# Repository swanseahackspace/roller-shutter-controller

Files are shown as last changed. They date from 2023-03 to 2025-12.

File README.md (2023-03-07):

# Table of Contents

- [Introduction](https://github.com/swanseahackspace/roller-shutter-controller/#introduction)
- [Hardware](https://github.com/swanseahackspace/roller-shutter-controller/#hardware)
- [Software](https://github.com/swanseahackspace/roller-shutter-controller/#software)
	- [Requirements](https://github.com/swanseahackspace/roller-shutter-controller/#requirements)
	- [Installation](https://github.com/swanseahackspace/roller-shutter-controller/#installation)
  
# Introduction
Roller Shutter RFID Access Control PCB. Uses an ESP-32-C3 (Lolin C3 Mini)

# Hardware

#### Enclosure
The PCB has been designed to fit into ide EL161 enclosure.

- [Technical Drawing](hardware/enclosure-dimensions.pdf)
- [Product Page](https://ide.es/eng/products/junction-boxes-and-mechanisms/ip65-ip67-junction-boxes/ref_EL161)

#### KiCad Renders
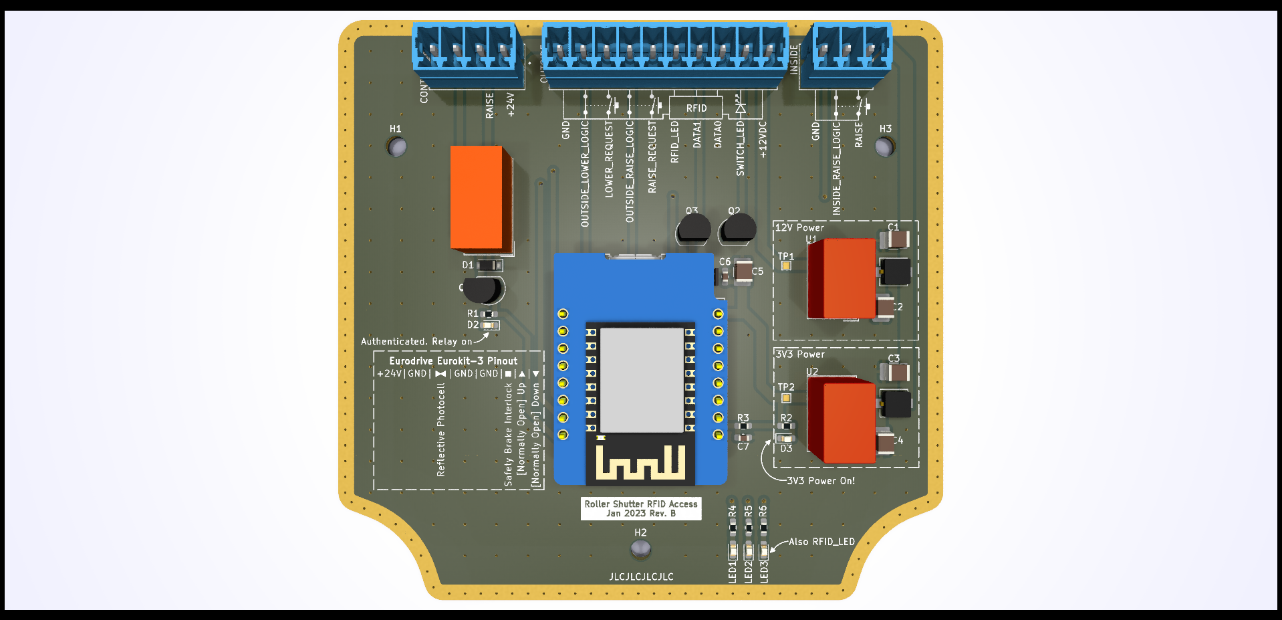
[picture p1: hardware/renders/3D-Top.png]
Top down 3D view

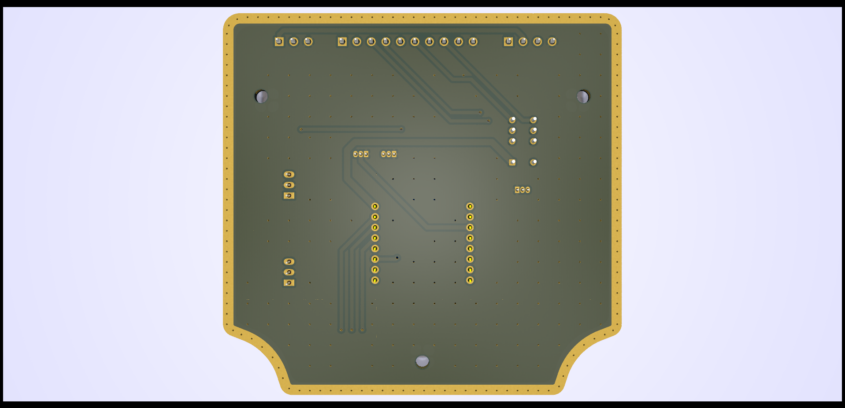
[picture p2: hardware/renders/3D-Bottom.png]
Bottom up 3D View


#### Assembly Render
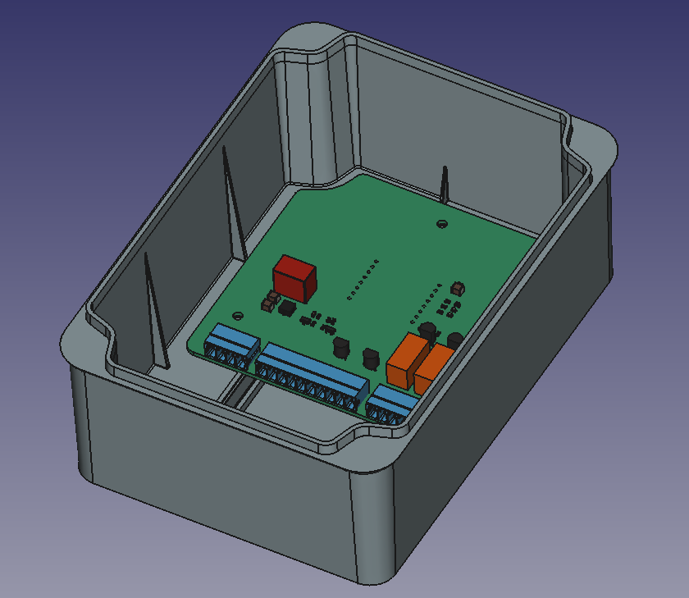
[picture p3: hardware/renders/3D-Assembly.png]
Assembly render


# Software
In the software folder you will find two programs:

- test is a simple script for doing hardware debugging. It provides a quick way to check that the LEDs are all working, and to toggle the relay on and off
- doorlock is a [submodule](https://git-scm.com/book/en/v2/Git-Tools-Submodules) of another git repo: https://github.com/swanseahackspace/doorlock. This is currently incompatable with this hardware, but will be modified to support both it's original hardware and the ESP-32-C3 via a flag in the config file.

### Requirements
- Arduino IDE or equivalent
- Arduino Libraries:
  - Adafruit Graphics
  - Adafruit SSD1306 Wemos Mini OLED

### Installation

1. Clone git repo
```
git clone https://github.com/swanseahackspace/roller-shutter-controller
```

2. Go into the doorlock directory
```
cd software/doorlock
```

3. Initialise the submodule
```
git submodule init
```

4. Update the submodule
```
git submodule update
```

5. Open .ino file in [Arduino IDE](https://www.arduino.cc/en/software)

6. Follow the [Wemos/Lolin C3 Mini Arduino development guide](https://www.wemos.cc/en/latest/tutorials/c3/get_started_with_arduino_c3.html)

7. Plug the board into your machine via the USB type-C port on the ESP-32-C3

8. Check the correct port is set in the Arduino IDE (Tools -> Port)

9. Upload the code to the ESP32

### Troubleshooting

*Errors uploading code to ESP-32-C3*
Use the following procedure:

- Hold on Button 9
- Press Button Reset
- Release Button 9 When you hear the prompt tone on usb reconnection

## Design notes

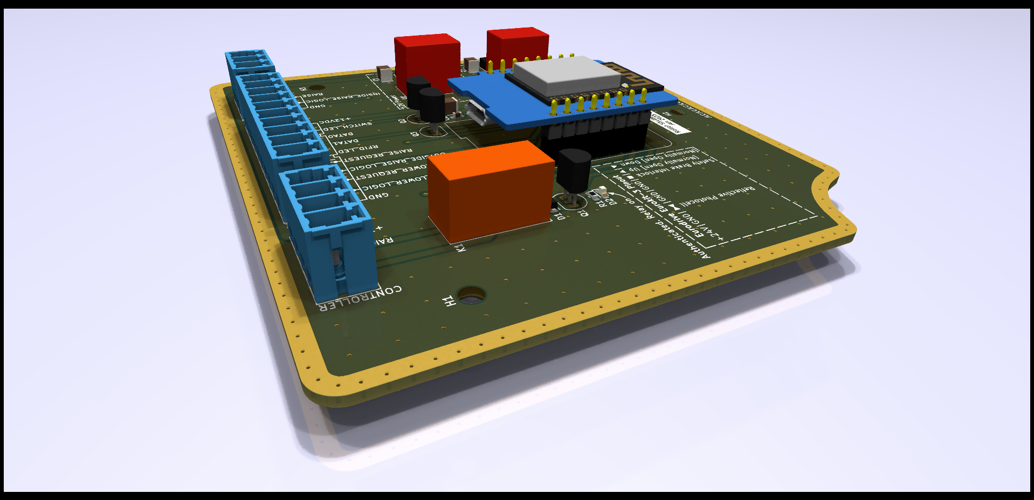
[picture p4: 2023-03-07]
hardware/renders/3D-3D.png

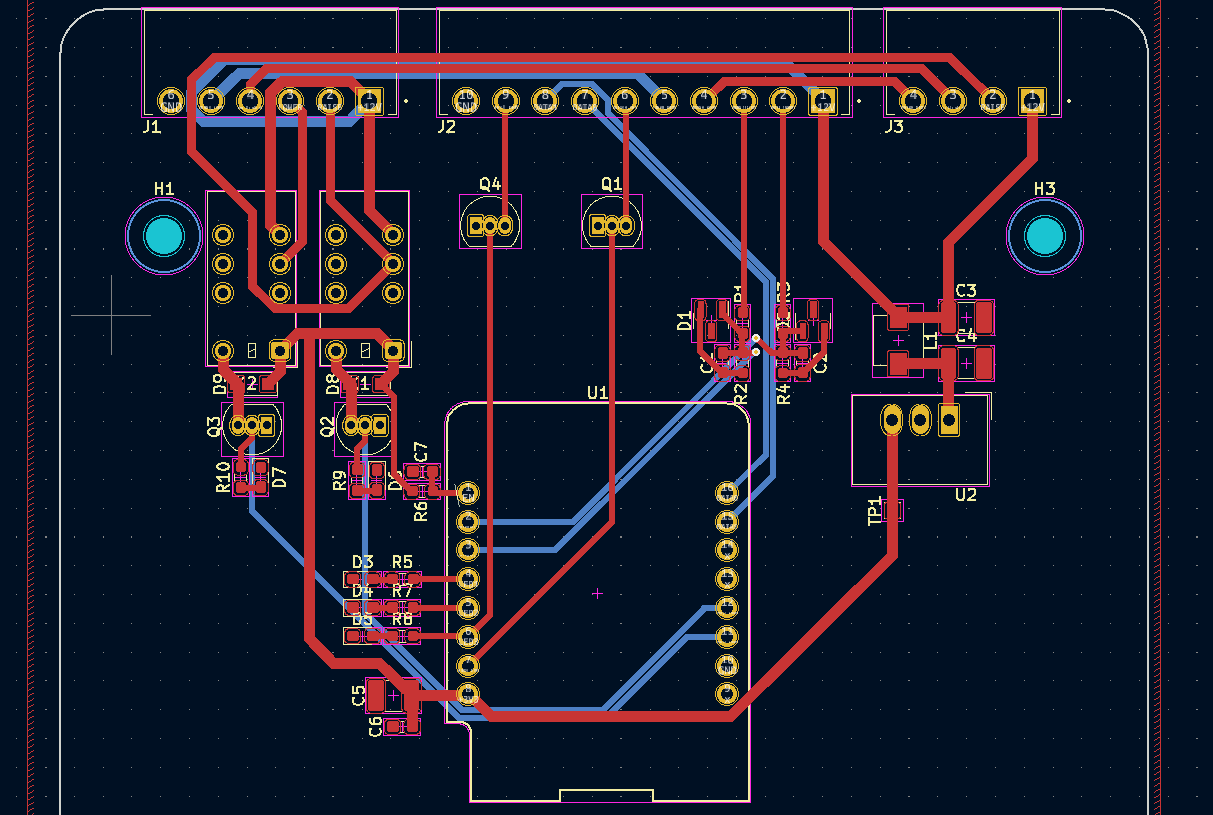
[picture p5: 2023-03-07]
hardware/renders/2D.png

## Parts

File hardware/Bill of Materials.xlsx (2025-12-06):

Reference(s) | Value | Price (Each) | PCB Qty | PCB (Total) | Order Qty | Order (Total) | Ordered? | Link | LibPart | Footprint | Datasheet | Notes
KiCad BOM
C1, C2 | 10nF | £0.03 | 2 | £0.06 | 10 | £0.29 | TRUE | https://www.digikey.co.uk/en/products/detail/kemet/C0603C103M5RAC7411/12701322 | Device:C |  | ~
C3, C4, C5 | 10uF | £0.61 | 3 | £1.83 | 10 | £6.10 | TRUE | https://www.digikey.co.uk/en/products/detail/kemet/C1210C106K5RAC7800/4918882 | Device:C |  | ~ | 50V
C6 | 0.1uF | £0.08 | 1 | £0.08 | 10 | £0.76 | TRUE | https://www.digikey.co.uk/en/products/detail/kemet/C0603C104K4RAC7081/6873865 | Device:C |  | ~
C7 | 1uF | £0.06 | 1 | £0.06 | 10 | £0.55 | TRUE | https://www.digikey.co.uk/en/products/detail/kemet/C0603C105K8PAC7411/12701126 | Device:C |  | ~
D1, D2 | D_Zener | £0.15 | 2 | £0.31 | 10 | £1.55 | TRUE | https://www.digikey.co.uk/en/products/detail/diodes-incorporated/MMBZ5226B-7-F/717773 | Device:D_Zener |  | ~
D3, D4, D5, D6, D7 | LED |  | 5 |  | 10 | £0.00 |  | Not Fitted | Device:LED |  | ~
D?-Red | Red LED Option | £0.16 | 1 | £0.16 | 10 | £1.56 | TRUE | https://www.digikey.co.uk/en/products/detail/w%C3%BCrth-elektronik/150060SS75000/4489903 | -
D?-Green | Green LED Option | £0.16 | 3 | £0.47 | 10 | £1.56 | TRUE | https://www.digikey.co.uk/en/products/detail/w%C3%BCrth-elektronik/150060GS75000/4489898 | -
D?-Blue | Blue LED Option | £0.18 | 1 | £0.18 | 10 | £1.80 | TRUE | https://www.digikey.co.uk/en/products/detail/w%C3%BCrth-elektronik/150060BS75000/4489895 | -
D8, D9 | 1N4007 | £0.14 | 2 | £0.27 | 10 | £1.37 | TRUE | https://www.digikey.co.uk/en/products/detail/smc-diode-solutions/1N4007FL/11657817 | Diode:1N4007 | Diode_THT:D_DO-41_SOD81_P10.16mm_Horizontal | http://www.vishay.com/docs/88503/1n4001.pdf
H1, H2, H3, H4 | MountingHole |  | 4 |  |  |  |  | - | Mechanical:MountingHole |  | ~
J1 | Screw_Terminal_01x06 | £1.18 | 1 | £1.18 | 2 | £2.35 | TRUE | https://www.digikey.co.uk/en/products/detail/cui-devices/TBP03R1-350-06BE/15775591 | Connector:Screw_Terminal_01x06 |  | ~
J2 | Screw_Terminal_01x10 | £1.49 | 1 | £1.49 | 2 | £2.98 | TRUE | https://www.digikey.co.uk/en/products/detail/cui-devices/TBP03R1-350-10BE/15775438 | Connector:Screw_Terminal_01x10 |  | ~
J3 | Screw_Terminal_01x04 | £0.78 | 1 | £0.78 | 2 | £1.56 | TRUE | https://www.digikey.co.uk/en/products/detail/cui-devices/TBP03R1-350-04BE/15775596 | Connector:Screw_Terminal_01x04 |  | ~
K3, K4 | EC2-3NU | £2.26 | 2 | £4.51 | 4 | £9.02 | TRUE | https://www.digikey.co.uk/en/products/detail/kemet/EC2-3NU/4291108?s=N4IgTCBcDaIKIGEwFoDMA5AqiAugXyA | Relay:EC2-3NU | Relay_THT:Relay_DPDT_Kemet_EC2 | https://content.kemet.com/datasheets/KEM_R7002_EC2_EE2.pdf
L1 | 5.6uH | £6.57 | 1 | £6.57 | 2 | £13.14 | TRUE | https://www.digikey.co.uk/en/products/detail/traco-power/TCK-141/9382093 | Device:L |  | https://docs.rs-online.com/1b0c/A700000008094192.pdf | TCK-141
Q1, Q2, Q3 | 2N7000 | £0.39 | 3 | £1.16 | 10 | £3.88 | TRUE | https://www.digikey.co.uk/en/products/detail/onsemi/2N7000/244278 | Transistor_FET:2N7000 | Package_TO_SOT_THT:TO-92_Inline | https://www.vishay.com/docs/70226/70226.pdf
R1, R3, R7 | 10k | £0.09 | 3 | £0.28 | 10 | £0.92 | TRUE | https://www.digikey.co.uk/en/products/detail/yageo/AA0603FR-0710KL/5888698 | Device:R |  | ~
R2, R4 | 3K9 | £0.02 | 2 | £0.04 | 10 | £0.22 | TRUE | https://www.digikey.co.uk/en/products/detail/yageo/RC0603FR-133K9L/14008250 | Device:R |  | ~
R5, R6, R8, R9, R10 | 220R | £0.02 | 5 | £0.11 | 20 | £0.43 | TRUE | https://www.digikey.co.uk/en/products/detail/yageo/RC0603FR-13220RL/14008234 | Device:R |  | ~
TP1 | TestPoint |  | 1 |  |  |  |  | - | Connector:TestPoint |  | ~
U1 | WeMos_C3_mini | £3.67 | 1 | £3.67 | 4 | £14.68 | TRUE | https://www.aliexpress.com/item/1005004740051202.html?scm_id=1007.13339.291025.0&scm-url=1007.13339.291025.0 | Custom:WeMos_C3_mini | Module:WEMOS_C3_mini | https://www.wemos.cc/en/latest/c3/c3_mini.html
U2 | TSR_1-2433 | £4.37 | 1 | £4.37 | 2 | £8.74 | TRUE | https://www.digikey.co.uk/en/products/detail/traco-power/TSR-1-2433E/12171286 | Regulator_Switching:TSR_1-2433 | Converter_DCDC:Converter_DCDC_TRACO_TSR-1_THT | http://www.tracopower.com/products/tsr1.pdf
 |  |  | Sub Total | £27.56 | Sub Total | £73.44
Misc Parts
Z1 | 10-way Terminal Block Plug | £2.81 | 1 | £2.81 | 1 | £2.81 | TRUE | https://www.digikey.co.uk/en/products/detail/cui-devices/TBP03P3-350-10BE/15775410 | -
Z2 | 6-way Terminal Block Plug | £1.97 | 1 | £1.97 | 1 | £1.97 | TRUE | https://www.digikey.co.uk/en/products/detail/cui-devices/TBP03P3-350-06BE/15775440 | -
Z3 | 4-way Terminal Block Plug | £1.31 | 1 | £1.31 | 1 | £1.31 | TRUE | https://www.digikey.co.uk/en/products/detail/cui-devices/TBP03P3-350-04BE/15775446 | -
S1 | 0.96" OLED | £1.09 | 1 | £1.09 | 1 | £1.09 |  | https://www.aliexpress.com/item/32957309383.html
 |  |  | Sub Total | £6.08 | Sub Total | £6.08
 |  |  |  |  | Digikey Total | £64.85
 |  |  | Grand Total | £33.64 | Grand Total | £79.53

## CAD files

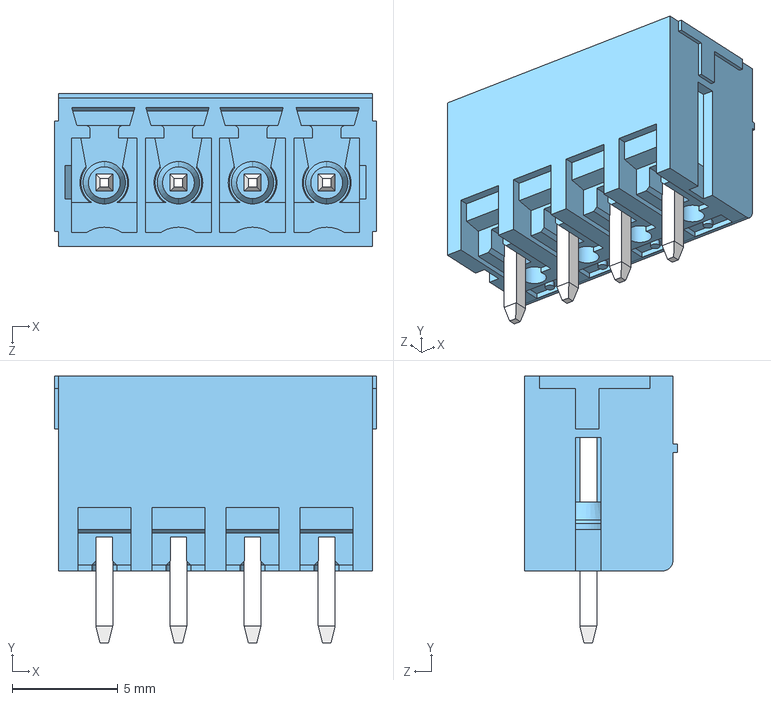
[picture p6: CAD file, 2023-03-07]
hardware/3dshapes/CUI_DEVICES_TBP03R2-350-04BE.step
15.2 x 12.6 x 7.20 mm

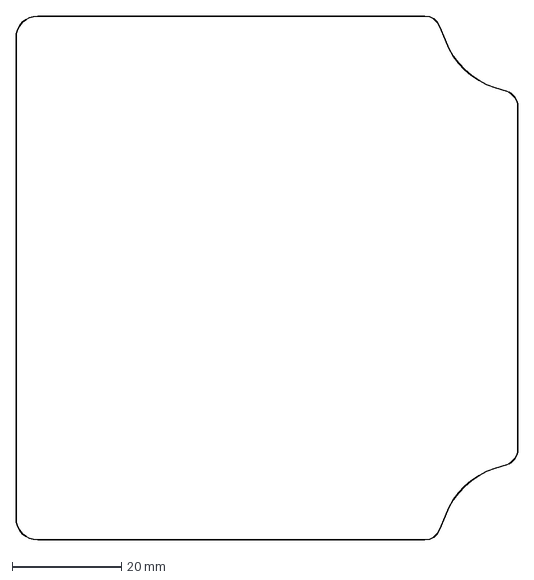
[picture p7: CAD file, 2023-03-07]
hardware/board_outline.dxf
92.0 x 96.0 mm

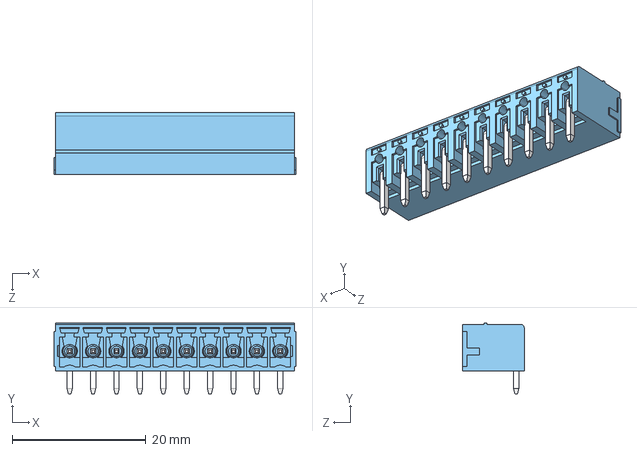
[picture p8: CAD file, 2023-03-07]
hardware/3dshapes/CUI_DEVICES_TBP03R1-350-10BE.step
36.2 x 10.6 x 9.20 mm

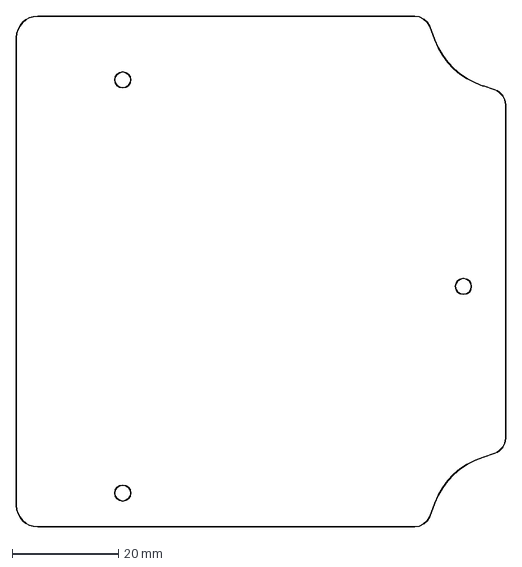
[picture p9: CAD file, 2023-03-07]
hardware/board_outline_and_mounting_holes.dxf
92.0 x 96.0 mm

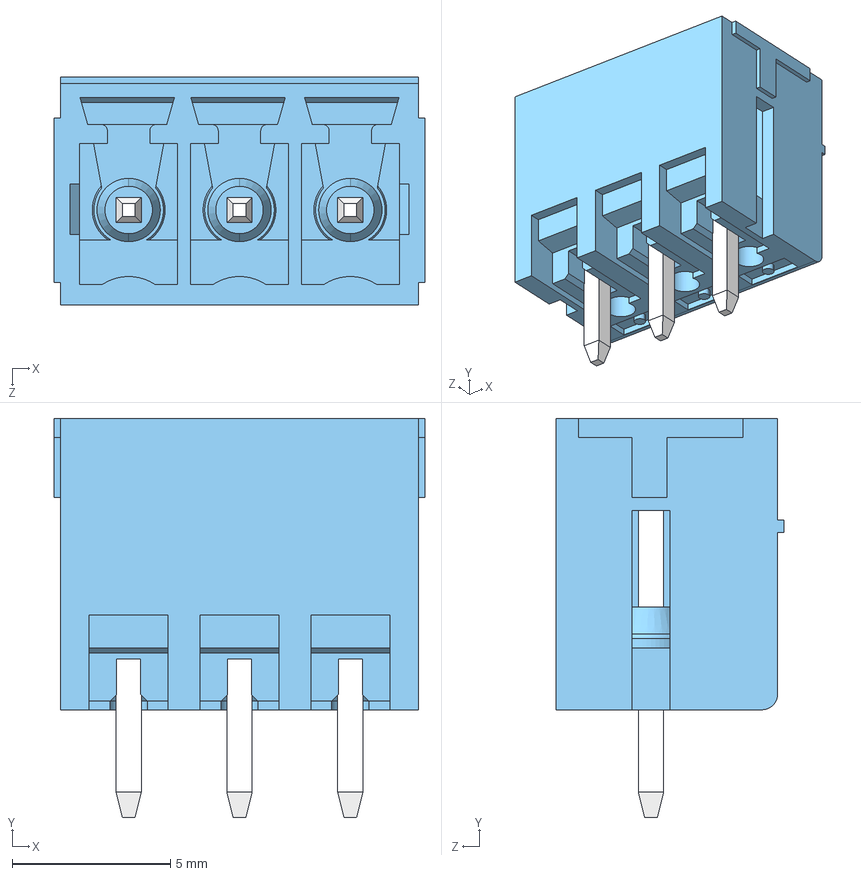
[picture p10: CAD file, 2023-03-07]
hardware/3dshapes/CUI_DEVICES_TBP03R2-350-03BE.step
11.7 x 12.6 x 7.20 mm

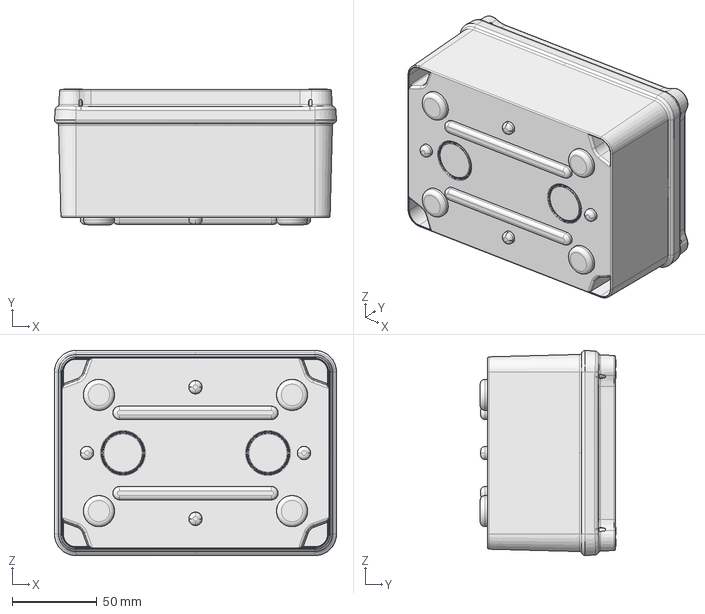
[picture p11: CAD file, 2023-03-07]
hardware/mechanical-design.FCStd
166.5 x 80.1 x 121.1 mm

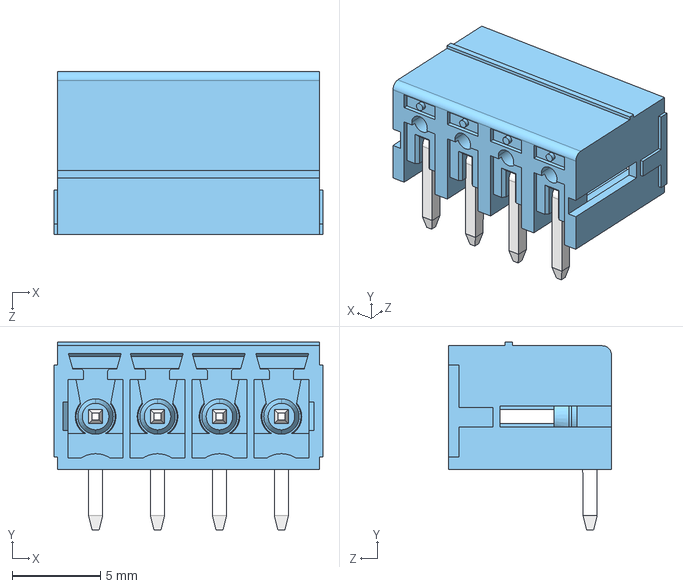
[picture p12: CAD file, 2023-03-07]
hardware/3dshapes/CUI_DEVICES_TBP03R1-350-04BE.step
15.2 x 10.6 x 9.20 mm

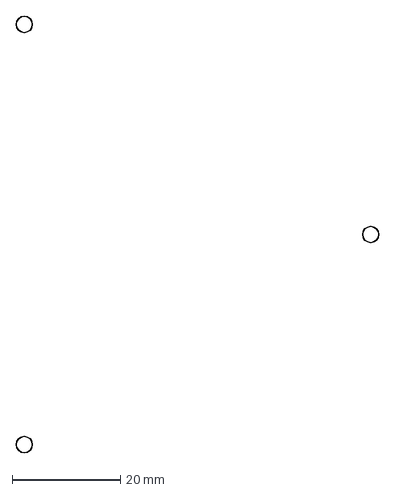
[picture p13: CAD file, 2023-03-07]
hardware/board_mounting_holes.dxf
67.1 x 80.7 mm

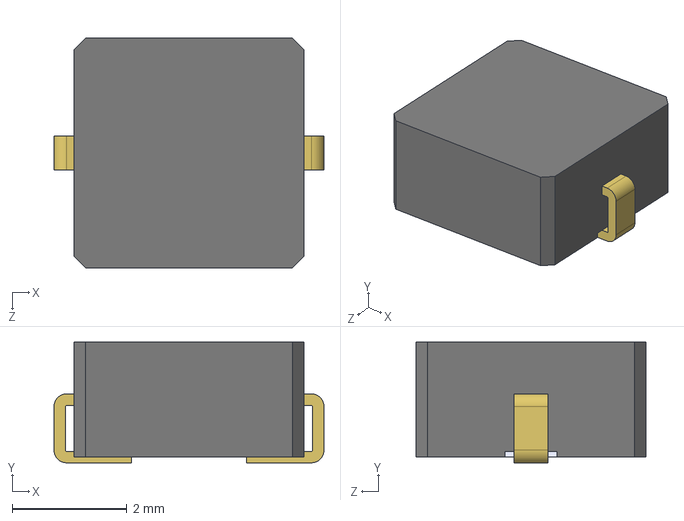
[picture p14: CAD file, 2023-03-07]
hardware/3dshapes/TCK-141.stp
4.70 x 2.10 x 4.00 mm

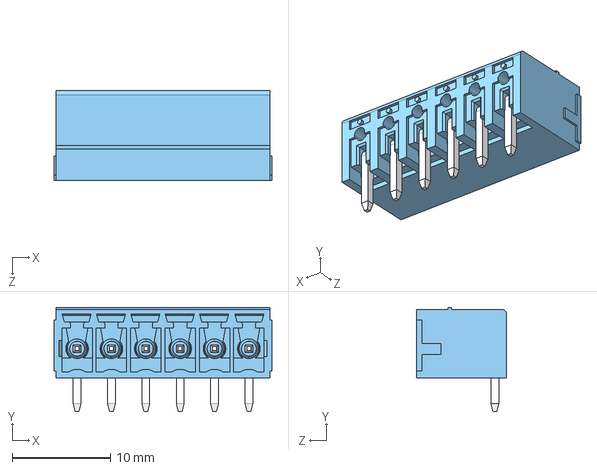
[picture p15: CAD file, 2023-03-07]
hardware/3dshapes/CUI_DEVICES_TBP03R1-350-06BE.step
22.2 x 10.6 x 9.20 mm

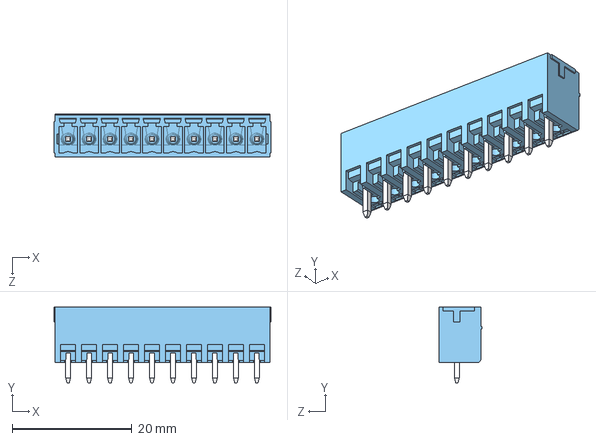
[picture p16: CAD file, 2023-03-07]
hardware/3dshapes/CUI_DEVICES_TBP03R2-350-10BE.step
36.2 x 12.6 x 7.20 mm

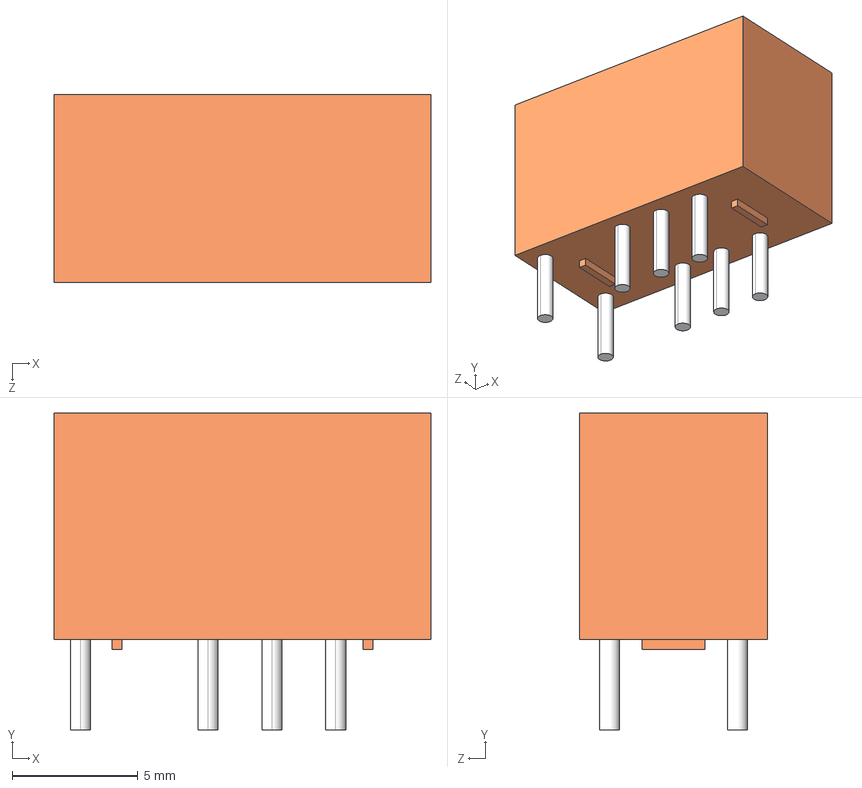
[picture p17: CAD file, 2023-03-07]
hardware/3dshapes/EC2-5NU--3DModel-STEP-56544.STEP
15.0 x 12.6 x 7.50 mm

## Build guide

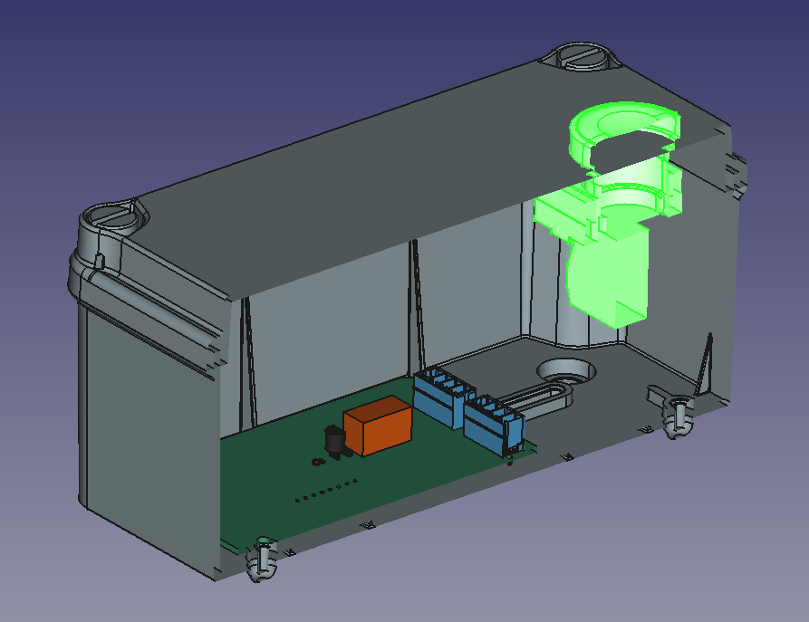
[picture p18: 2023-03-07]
hardware/renders/3D-Assembly-Button.png

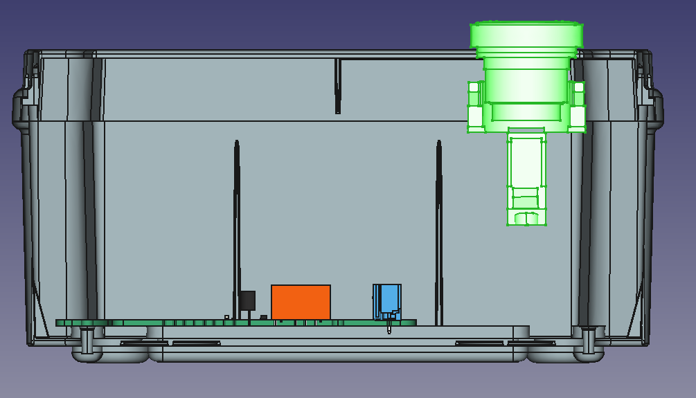
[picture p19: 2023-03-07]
hardware/renders/3D-Assembly-Button-2.png

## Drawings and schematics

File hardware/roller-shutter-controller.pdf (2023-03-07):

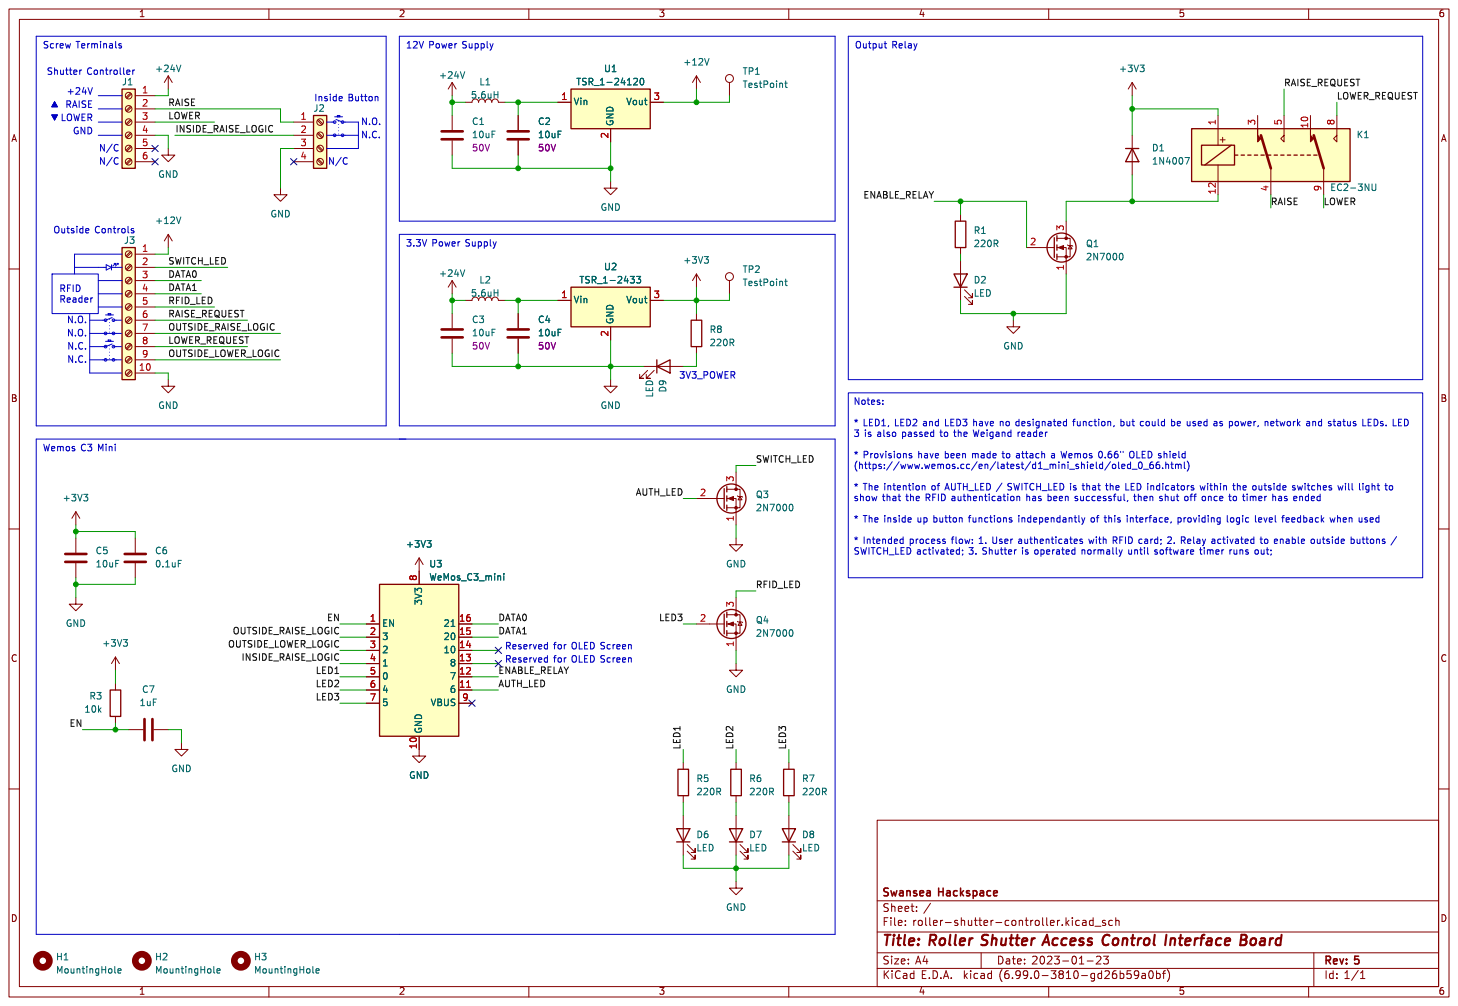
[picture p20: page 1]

Screw Terminals Wemos C3 Mini +24V N.O. N.O. RFID

3 is also passed to the Weigand reader * Provisions have been made to attach a Wemos 0.66" OLED shield

(https://www.wemos.cc/en/latest/d1_mini_shield/oled_0_66.html)

* The intention of AUTH_LED / SWITCH_LED is that the LED indicators within the outside switches will light to
show that the RFID authentication has been successful, then shut off once to timer has ended

* The inside up button functions independantly of this interface, providing logic level feedback when used

* Intended process flow: 1. User authenticates with RFID card; 2. Relay activated to enable outside buttons /

Reserved for OLED Screen

File: roller-shutter-controller.kicad_sch Sheet: / Swansea Hackspace

Id: 1/1 Title: Roller Shutter Access Control Interface Board

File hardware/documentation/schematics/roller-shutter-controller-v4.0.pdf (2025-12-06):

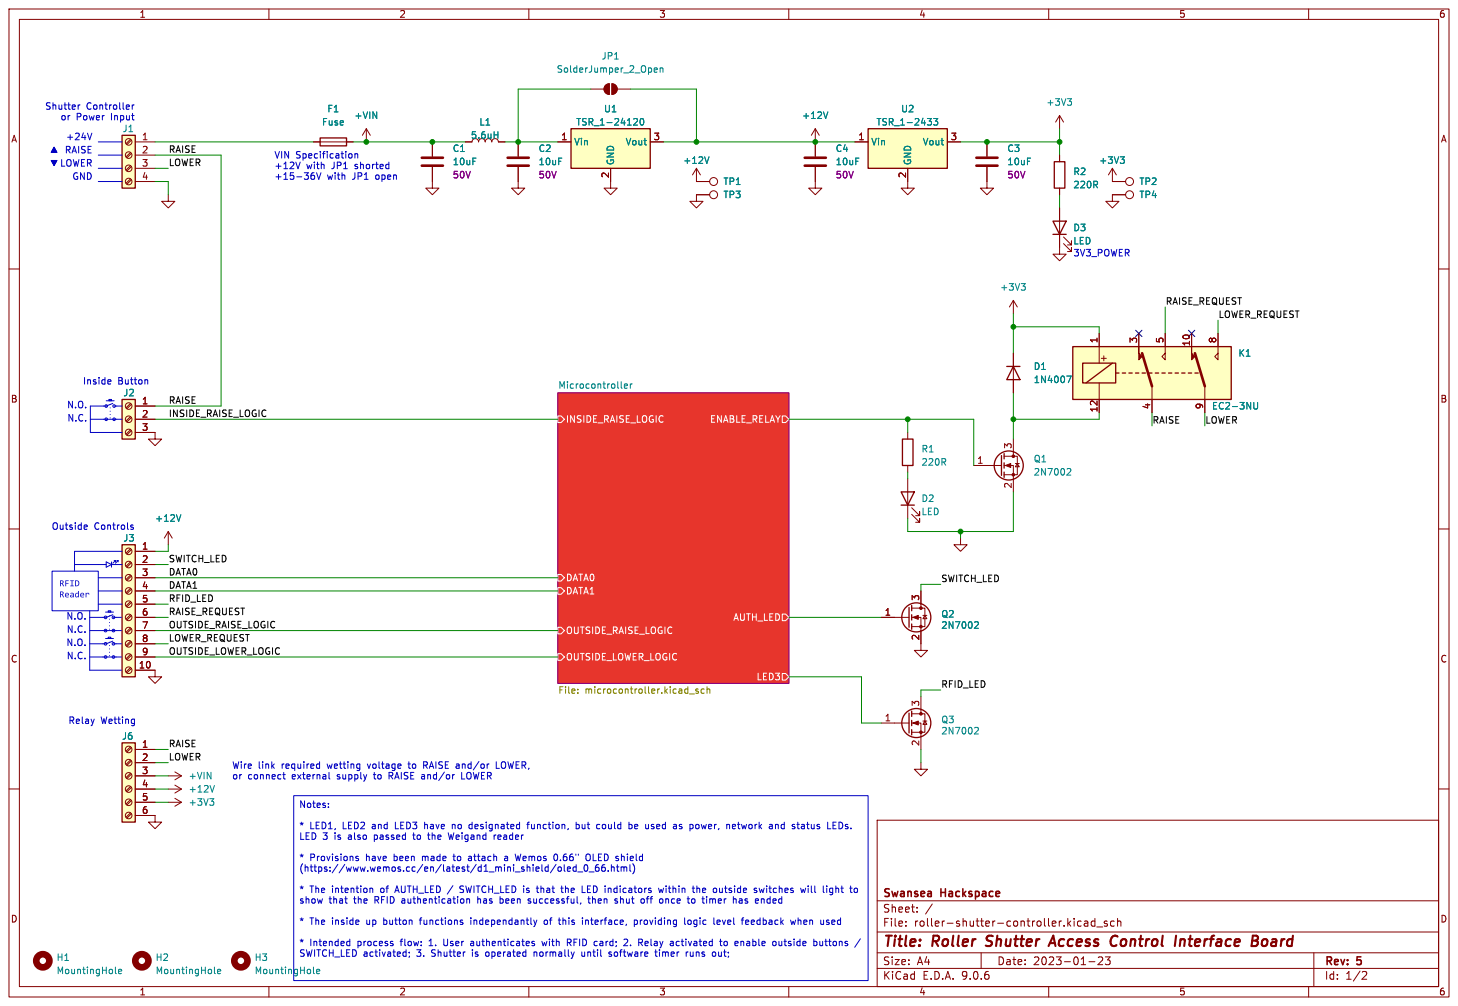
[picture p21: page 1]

+24V N.C. N.O. N.C. Relay Wetting
þÿ%² GND
RAISE Outside Controls RFID
LOWER

Id: 1/2 Title: Roller Shutter Access Control Interface Board

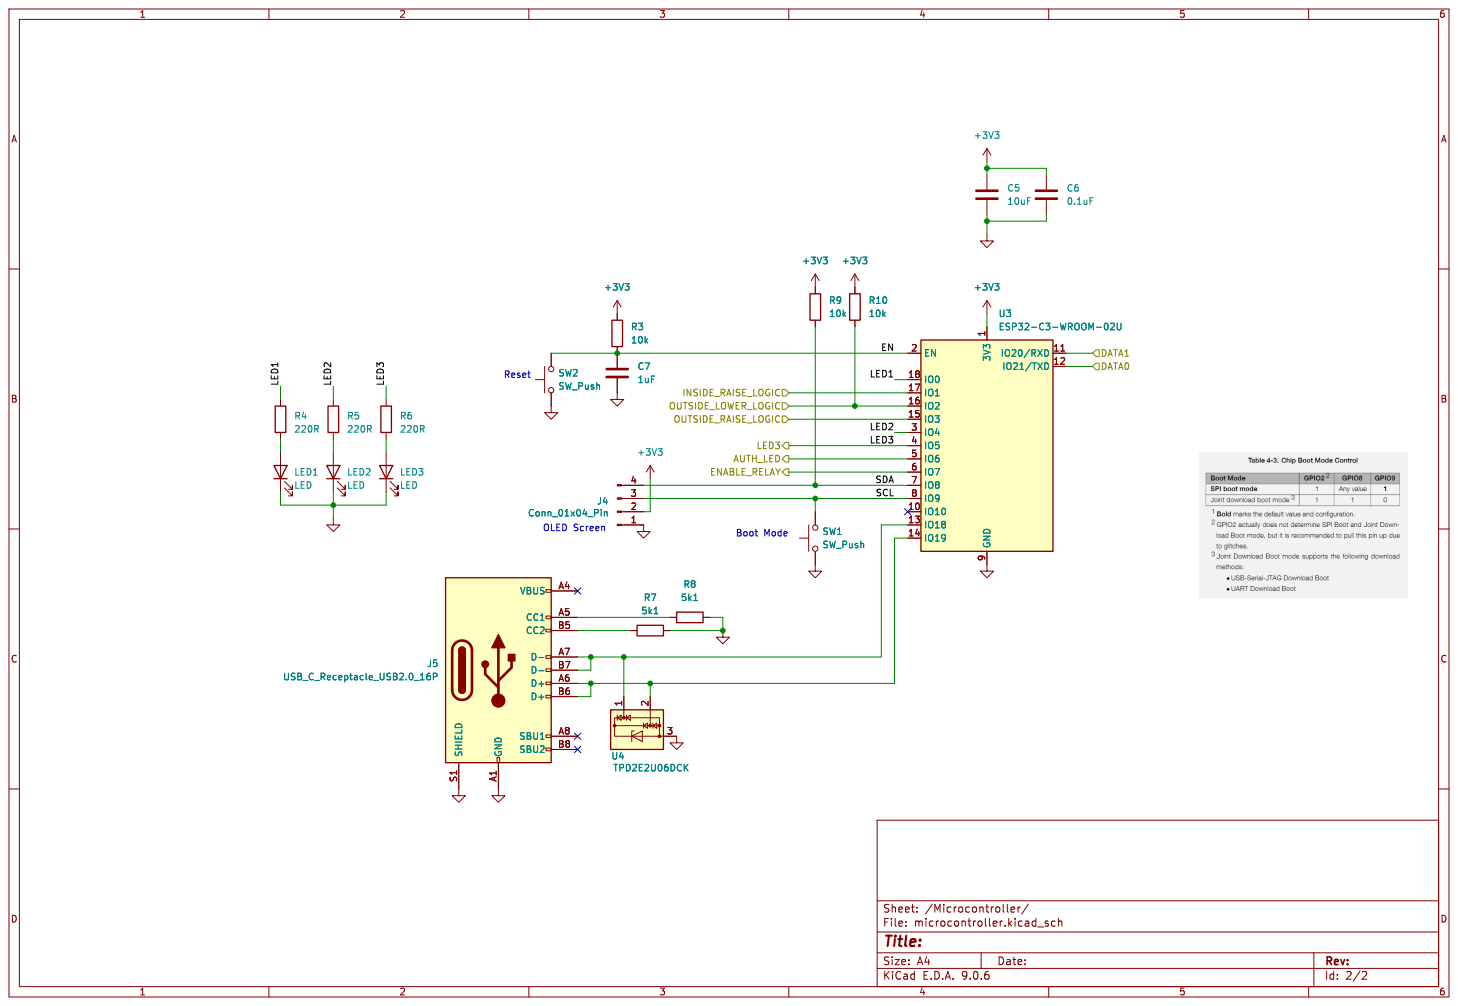
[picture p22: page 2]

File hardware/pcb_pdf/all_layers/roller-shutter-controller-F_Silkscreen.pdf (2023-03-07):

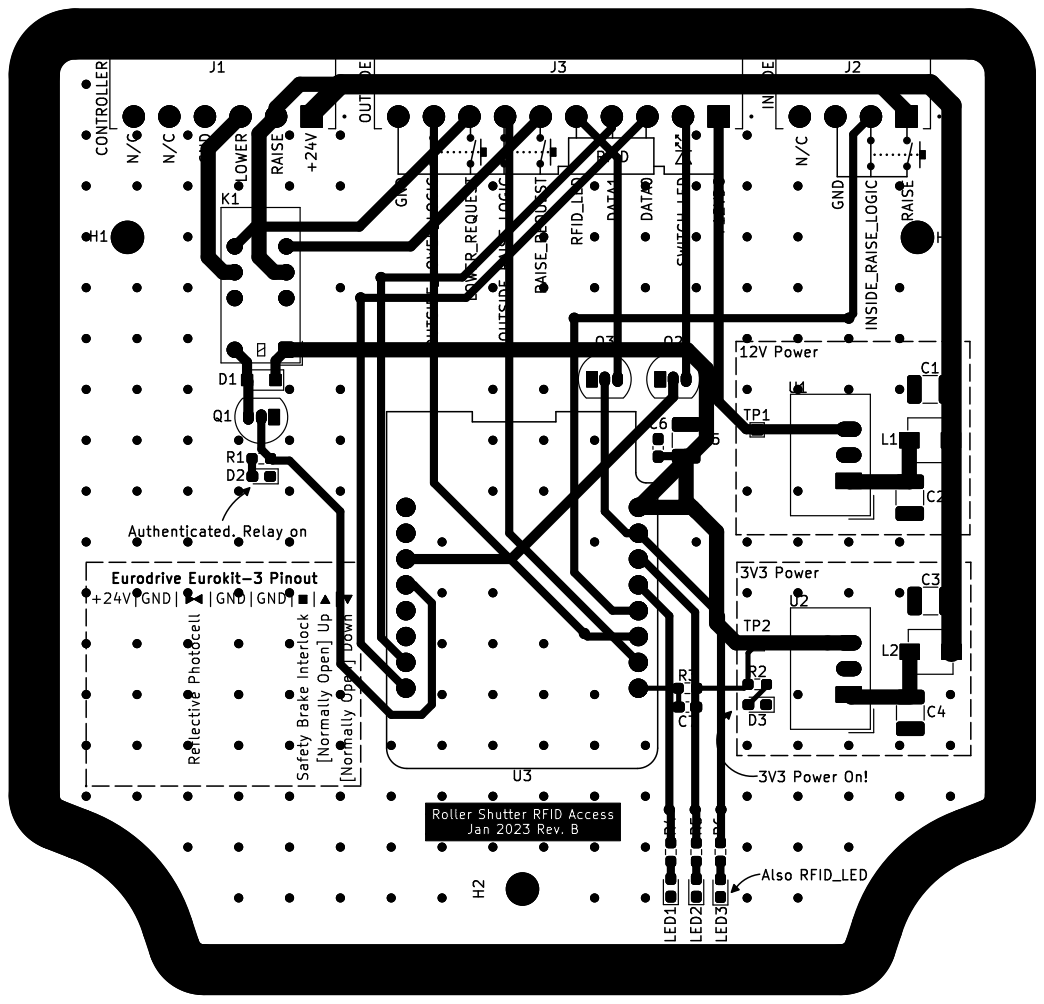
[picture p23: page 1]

[Normally Open] Down [Normally Open] Up Safety Brake Interlock Reflective Photocell þÿ+24V|GND|    |GND|GND|% |%²|%¼ þÿ%¼ þÿ%² Eurodrive Eurokit-3 Pinout Authenticated. Relay on Also RFID_LED

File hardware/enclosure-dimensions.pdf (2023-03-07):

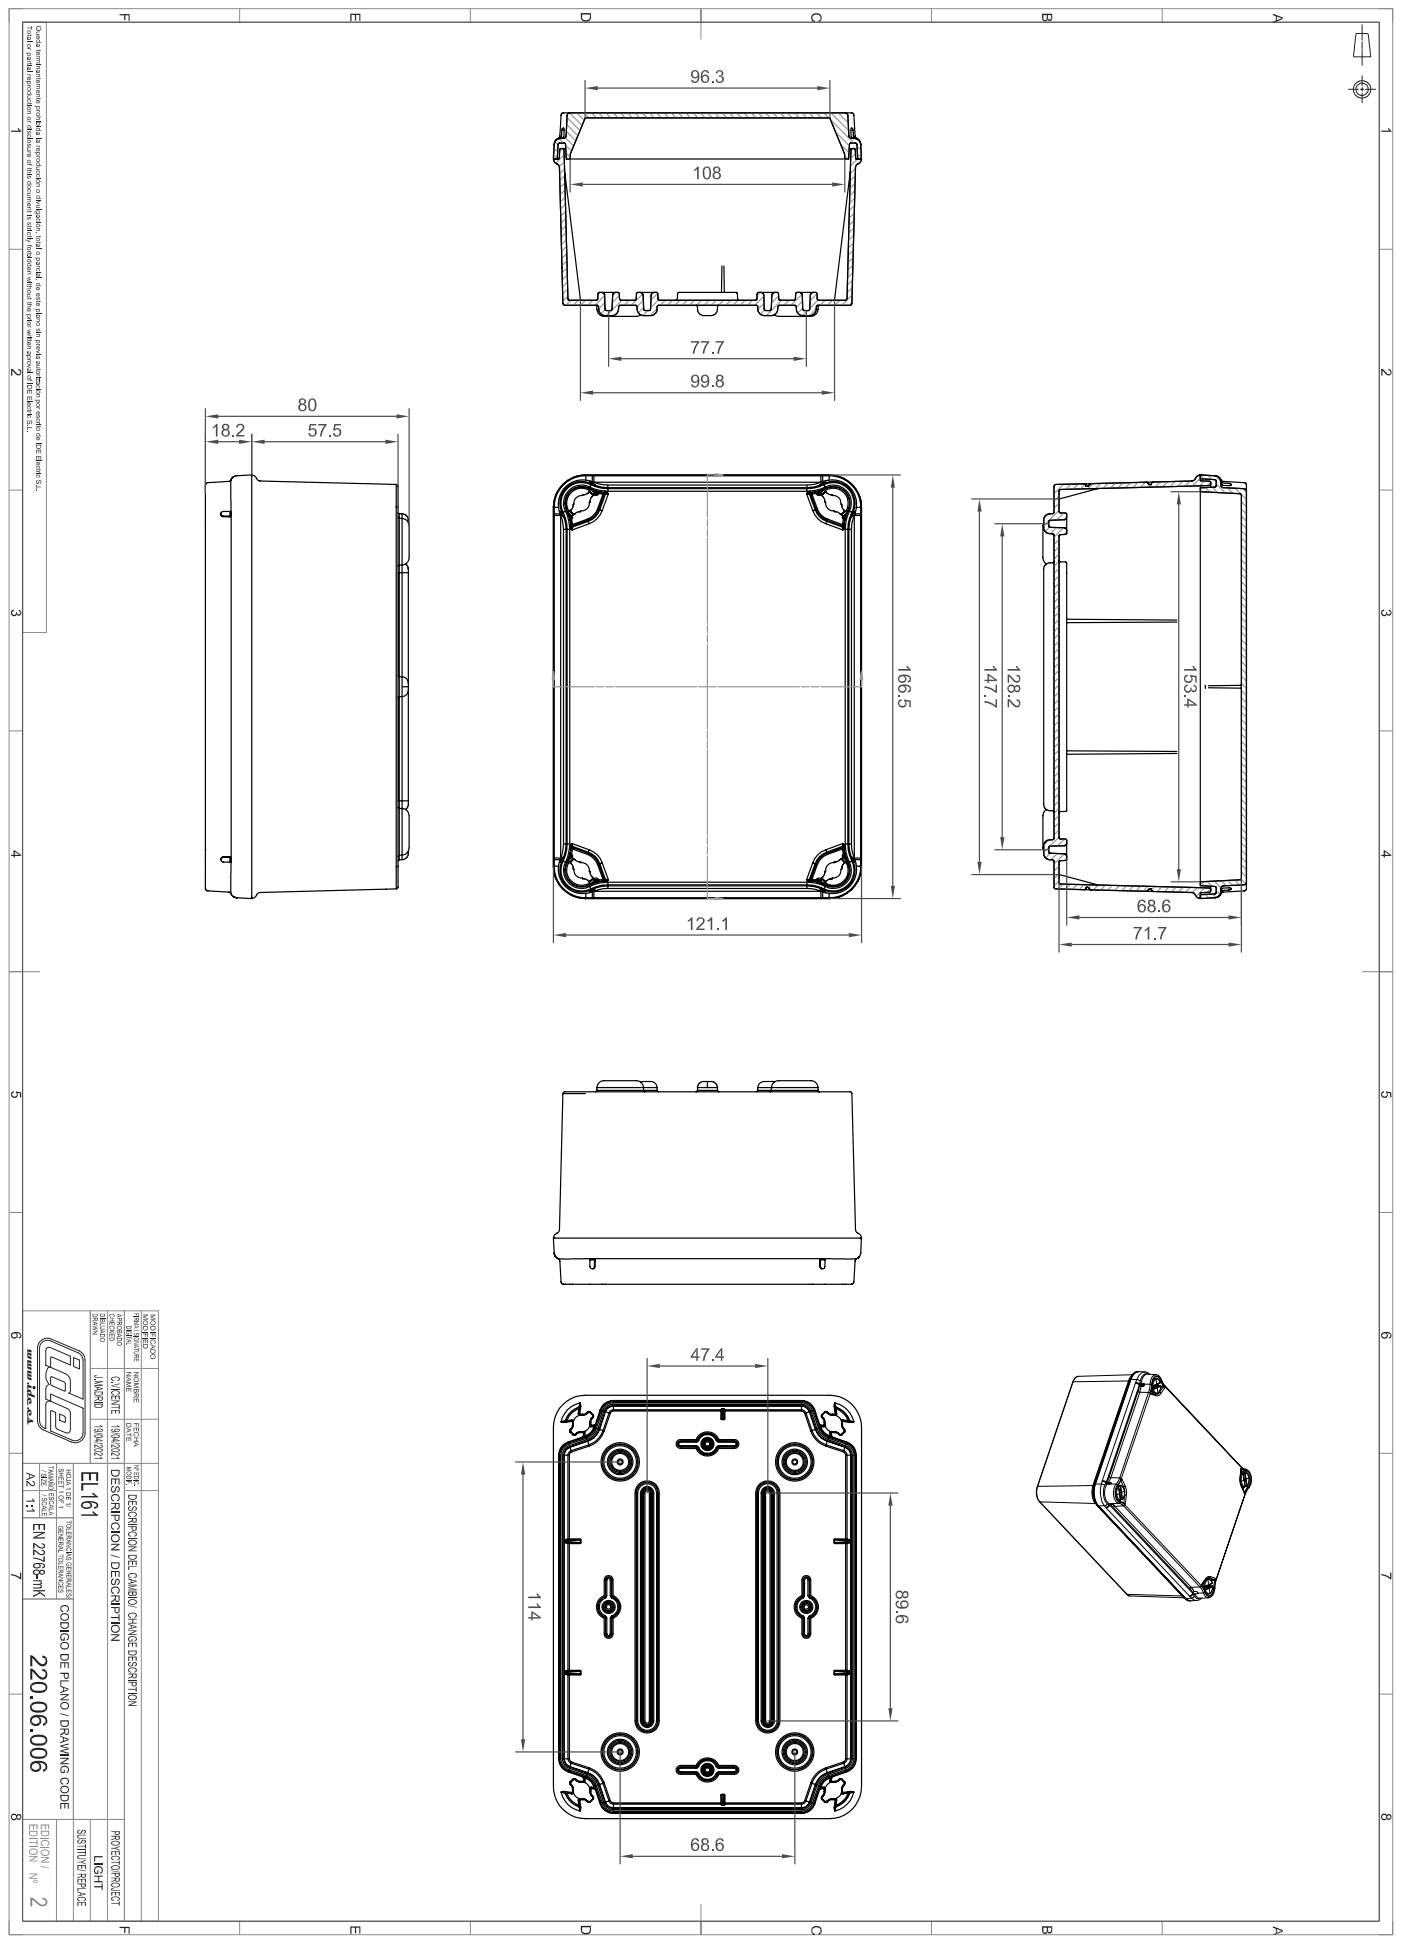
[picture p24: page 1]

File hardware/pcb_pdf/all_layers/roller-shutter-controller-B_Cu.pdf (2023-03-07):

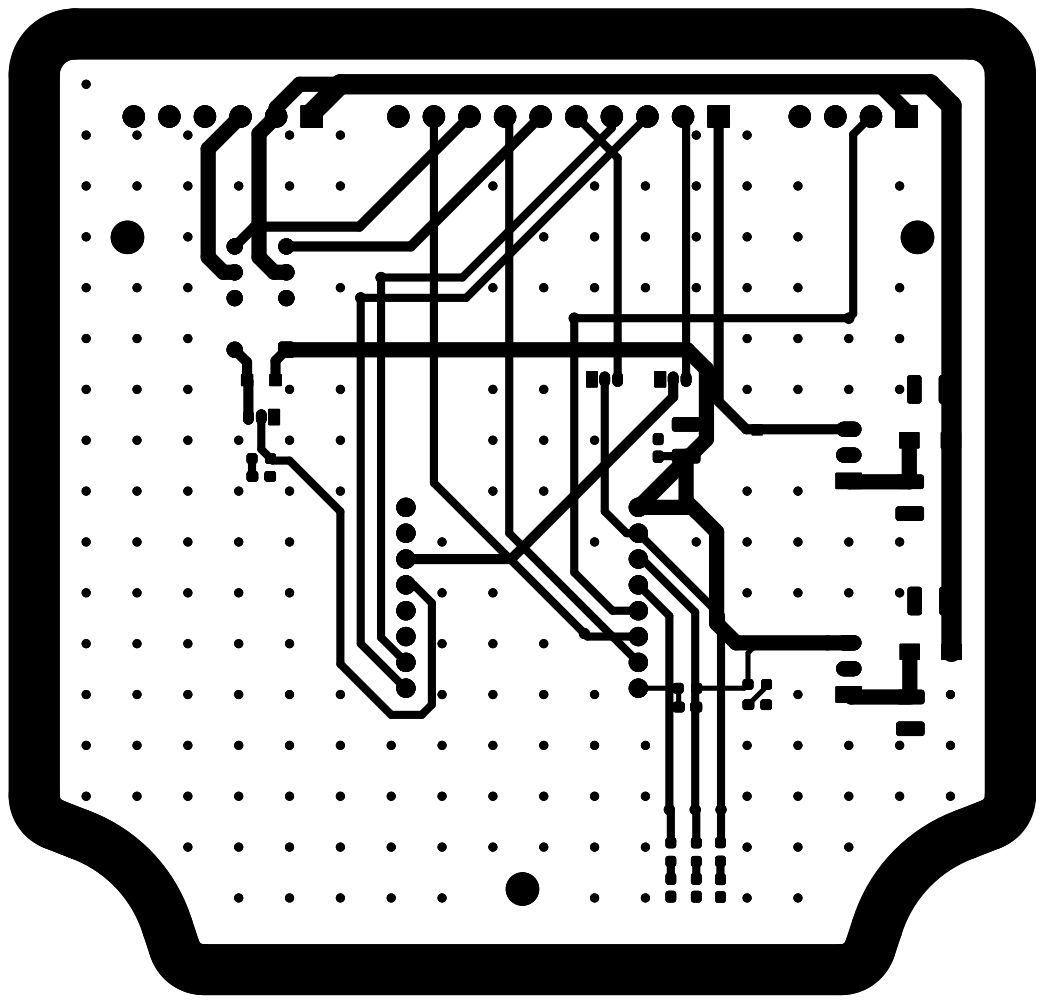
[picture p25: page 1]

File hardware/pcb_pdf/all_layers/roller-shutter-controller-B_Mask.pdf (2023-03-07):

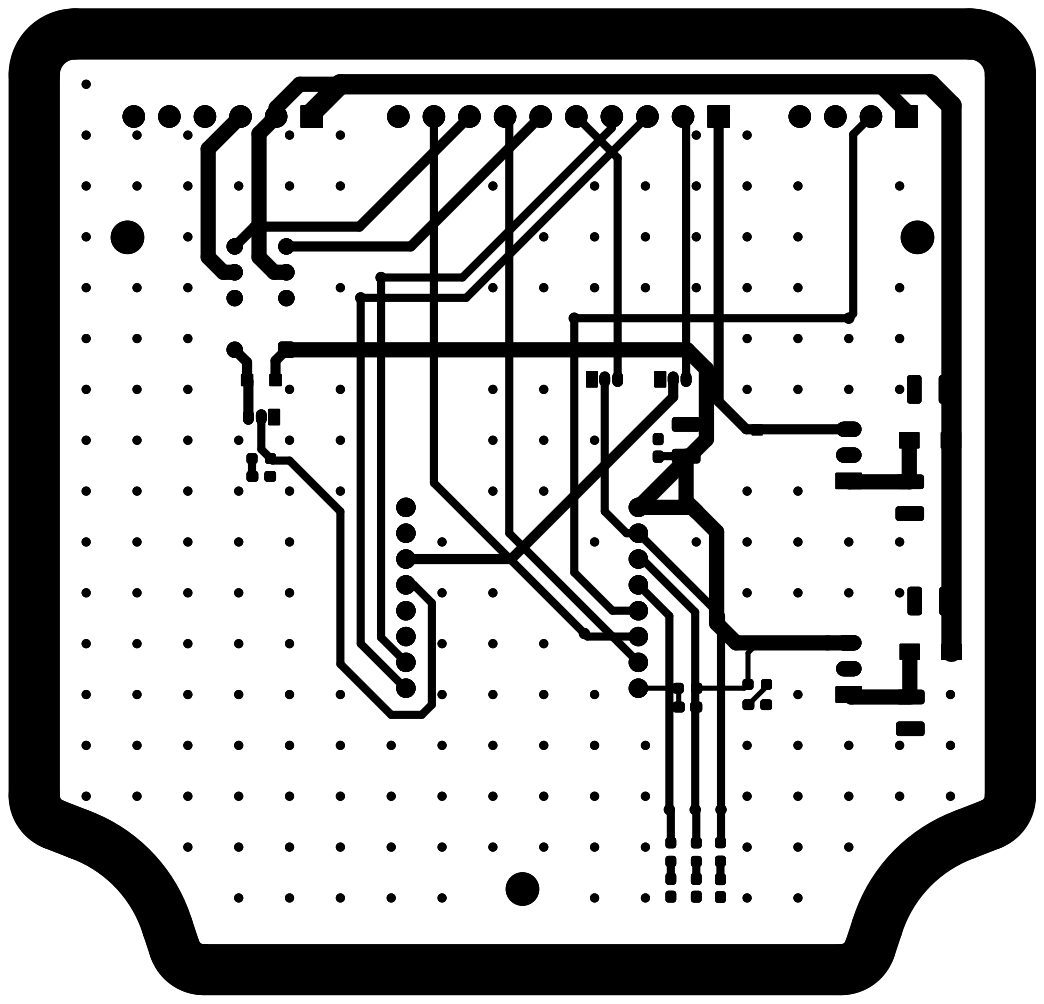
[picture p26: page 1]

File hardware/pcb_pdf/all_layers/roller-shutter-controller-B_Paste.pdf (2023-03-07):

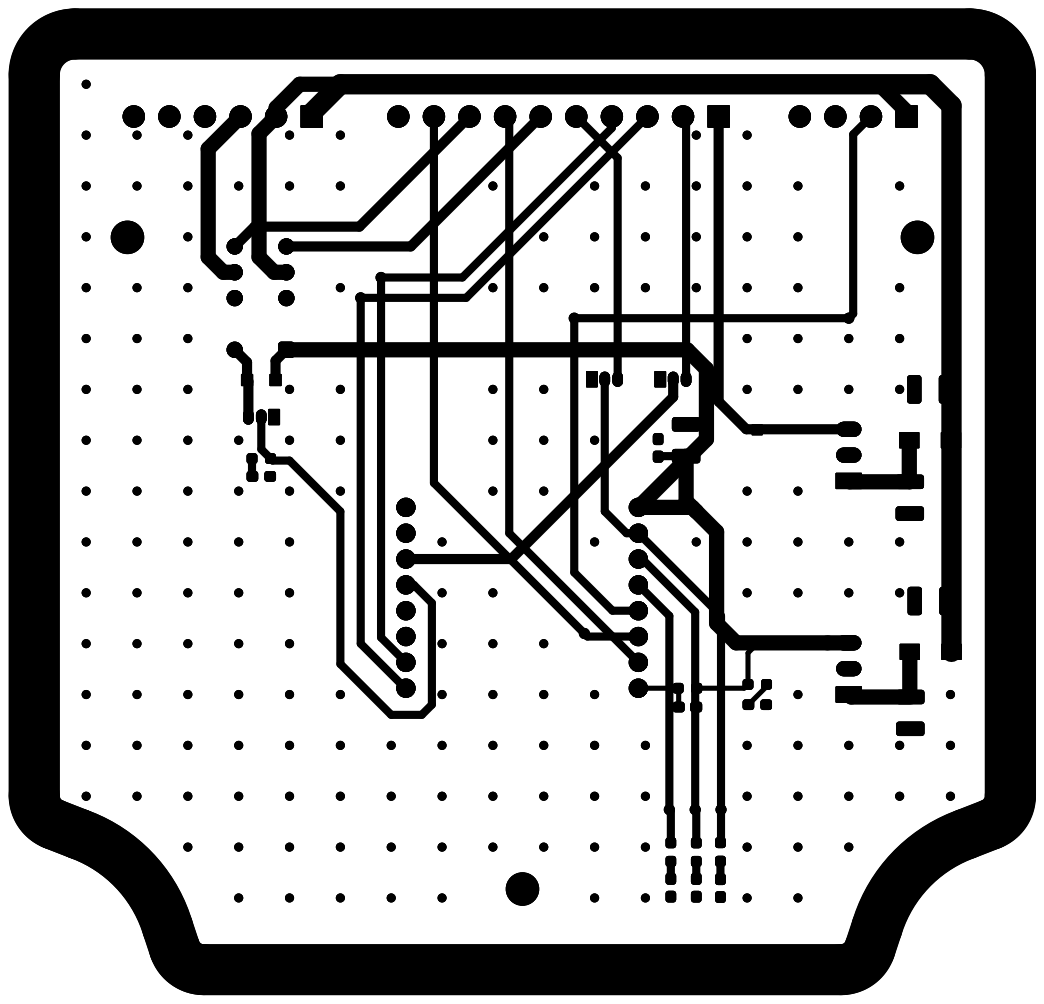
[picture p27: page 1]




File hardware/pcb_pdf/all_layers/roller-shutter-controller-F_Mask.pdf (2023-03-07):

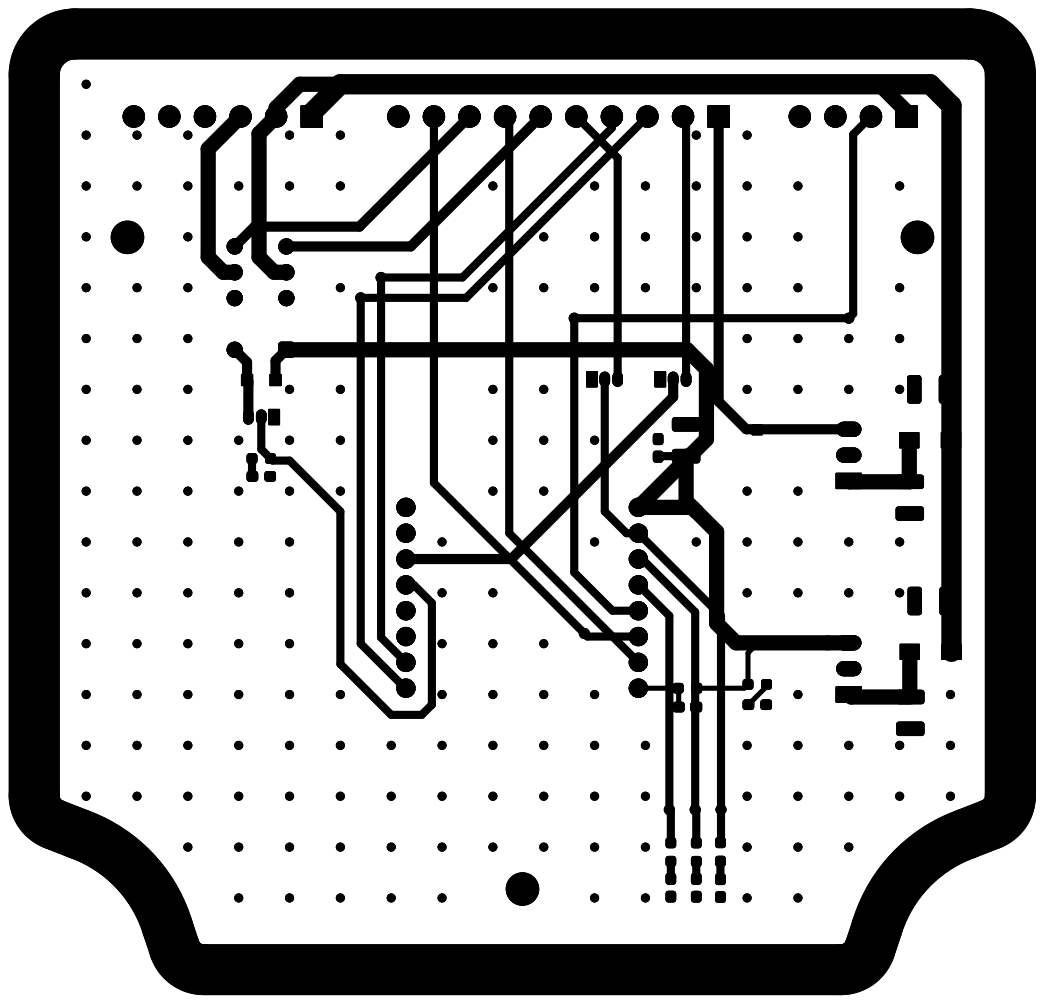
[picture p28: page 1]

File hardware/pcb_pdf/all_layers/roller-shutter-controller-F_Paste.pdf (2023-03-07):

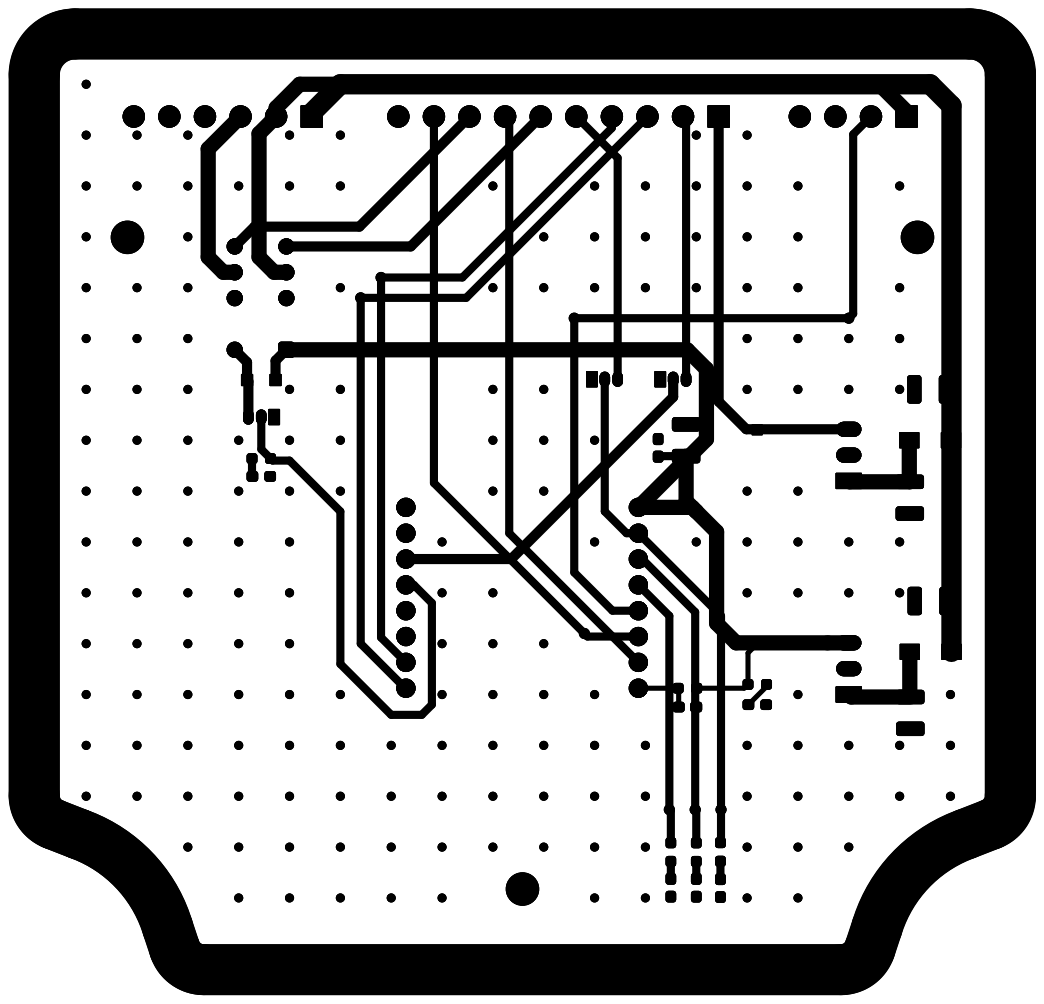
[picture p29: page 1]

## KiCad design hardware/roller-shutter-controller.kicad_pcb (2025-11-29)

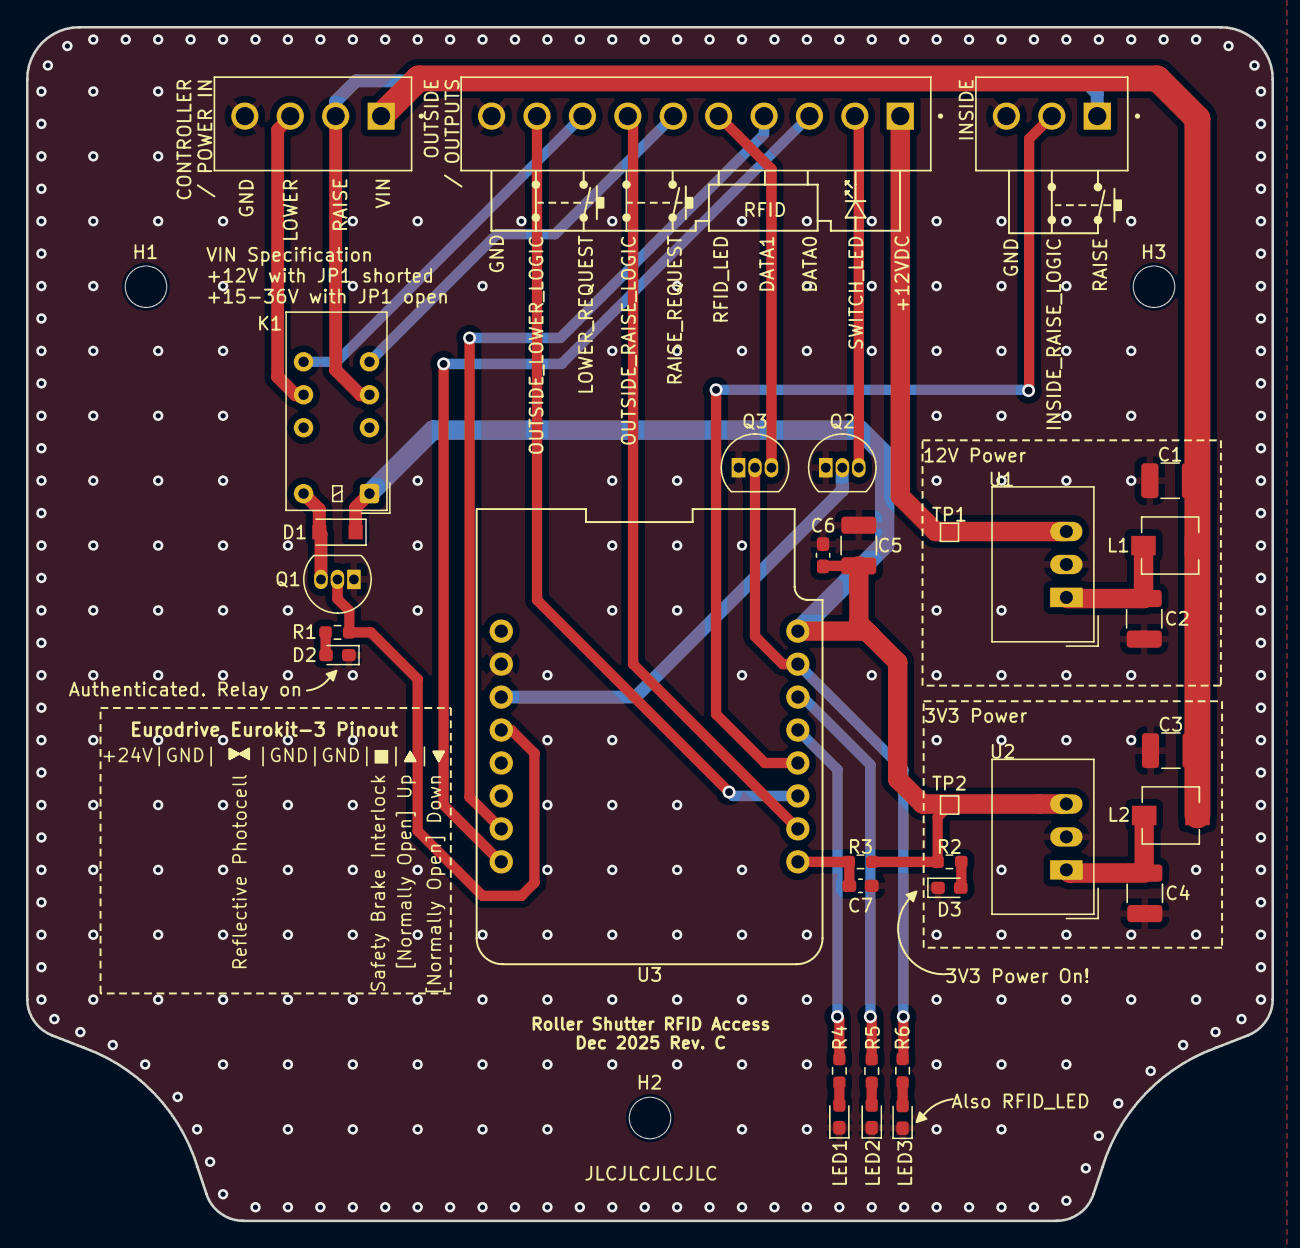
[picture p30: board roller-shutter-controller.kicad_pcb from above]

Board: 2 copper layers, 96.0 x 92.0 mm, 36 parts (0 on the bottom side), 29 nets.

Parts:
C1, C2, C3, C4, C5: 10uF; C_1210_3225Metric_Pad1.33x2.70mm_HandSolder
C6: 0.1uF; C_0603_1608Metric_Pad1.08x0.95mm_HandSolder
C7: 1uF; C_0603_1608Metric_Pad1.08x0.95mm_HandSolder
D1: 1N4007; D_SOD-123F
D2, D3: LED; LED_0603_1608Metric_Pad1.05x0.95mm_HandSolder
H1, H2, H3: MountingHole; MountingHole_3.2mm_M3
J1: Screw_Terminal_01x06; CUI_TBP03R2-350-04BE
J2: Screw_Terminal_01x04; CUI_TBP03R2-350-03BE
J3: Screw_Terminal_01x10; CUI_TBP03R2-350-10BE
K1: EC2-3NU; Relay_DPDT_Kemet_EC2
L1, L2: 5.6uH; L_TracoPower_TCK-141
LED1, LED2, LED3: LED; LED_0603_1608Metric_Pad1.05x0.95mm_HandSolder
Q1, Q2, Q3: 2N7000; TO-92_Inline
R1, R2, R4, R5, R6: 220R; R_0603_1608Metric_Pad0.98x0.95mm_HandSolder
R3: 10k; R_0603_1608Metric_Pad0.98x0.95mm_HandSolder
TP1, TP2: TestPoint; TestPoint_Pad_1.0x1.0mm
U1: TSR_1-24120; Converter_DCDC_TRACO_TSR-1_THT
U2: TSR_1-2433; Converter_DCDC_TRACO_TSR-1_THT
U3: WeMos_C3_mini; wemos-d1-mini-with-pin-header-and-connector

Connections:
+3V3: C5.1, C6.1, D1.1 (K), K1.1, R2.2, R3.1, TP2.1, U2.3 (Vout), U3.8 (3V3)
+12V: J3.1, TP1.1, U1.3 (Vout)
+24V: C1.1, C3.1, J1.1, L1.1, L2.1
/AUTH_LED: Q2.2 (G), U3.11 (6)
/DATA0: J3.3, U3.16 (21)
/DATA1: J3.4, U3.15 (20)
/EN: C7.2, R3.2, U3.1 (EN)
/ENABLE_RELAY: Q1.2 (G), R1.2, U3.12 (7)
/INSIDE_RAISE_LOGIC: J2.2, U3.4 (1)
/LED1: R4.2, U3.5 (0)
/LED2: R5.2, U3.6 (4)
/LED3: Q3.2 (G), R6.2, U3.7 (5)
/LOWER: J1.3, K1.9
/LOWER_REQUEST: J3.8, K1.8
/OUTSIDE_LOWER_LOGIC: J3.9, U3.3 (2)
/OUTSIDE_RAISE_LOGIC: J3.7, U3.2 (3)
/RAISE: J1.2, J2.1, K1.4
/RAISE_REQUEST: J3.6, K1.5
/RFID_LED: J3.5, Q3.3 (D)
/SWITCH_LED: J3.2, Q2.3 (D)
GND: C1.2, C2.2, C3.2, C4.2, C5.2, C6.2, C7.1, D2.1 (K), D3.1 (K), J1.4, J2.3, J3.10, LED1.1 (K), LED2.1 (K), LED3.1 (K), Q1.1 (S), Q2.1 (S), Q3.1 (S), U1.2 (GND), U2.2 (GND), U3.10 (GND)
unnamed: D1.2 (A), K1.12, Q1.3 (D)
unnamed: D2.2 (A), R1.1
unnamed: D3.2 (A), R2.1
unnamed: LED1.2 (A), R4.1
unnamed: LED2.2 (A), R5.1
unnamed: LED3.2 (A), R6.1
unnamed: C2.1, L1.2, U1.1 (Vin)
unnamed: C4.1, L2.2, U2.1 (Vin)

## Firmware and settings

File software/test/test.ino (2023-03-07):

/* Roller Shutter Controller - Test Software
  - WHAT IT DOES
   Checks the hardware is working correctly for easier debugging.
   Once the startup sequence has completed, the current uptime is shown on the screen.
   In this screen, press the button on the ESP32 module (pin 9) to toggle the relay on or off
*/

/*-----( Import needed libraries )-----*/
#include <SPI.h>
#include <Wire.h>
#include <Adafruit_GFX.h>
#include <Adafruit_SSD1306.h>

/*-----( Declare Constants and Pin Numbers )-----*/
const int brightnessLED = 20; //LED PWM Value up to 255
const long debounceDelay = 500;    // the debounce time; increase if the output flickers

#define LED1 0
#define LED2 4
#define LED3 5
#define authLED 6
#define enableRelay 7
#define data0 21
#define data1 20
#define insideRaiseLogic 1
#define outsideRaiseLogic 3
#define outsideLowerLogic 2
#define button 9

static const unsigned char PROGMEM logo_bmp[] =
{ 0xff, 0xff, 0xff, 0xff, 0xff, 0xff, 0xff, 0xff, 0xe0, 0x07, 0xff, 0xff, 0xff, 0xfe, 0x00, 0x00,
  0x7f, 0xff, 0xff, 0xf8, 0x05, 0xa0, 0x1f, 0xff, 0xff, 0xf0, 0x7f, 0xfe, 0x0f, 0xff, 0xff, 0xc1,
  0xff, 0xff, 0x83, 0xff, 0xff, 0x87, 0xfe, 0x7f, 0xe1, 0xff, 0xff, 0x0f, 0xfc, 0x3f, 0xf0, 0xff,
  0xfe, 0x3f, 0xf8, 0x1f, 0xfc, 0x7f, 0xfc, 0x7f, 0xf0, 0x0f, 0xfe, 0x3f, 0xf8, 0xff, 0xe0, 0x07,
  0xfe, 0x1f, 0xf8, 0xff, 0xc0, 0x07, 0xff, 0x1f, 0xf1, 0xff, 0x80, 0x07, 0xff, 0x8f, 0xe3, 0xff,
  0x00, 0x03, 0xff, 0xc7, 0xe3, 0xff, 0x00, 0x01, 0xff, 0xc7, 0xc7, 0xfd, 0x80, 0x00, 0xff, 0xe7,
  0xc7, 0xf9, 0x80, 0x00, 0x7f, 0xe3, 0xcf, 0xf0, 0xe0, 0x00, 0x3f, 0xe3, 0xcf, 0xe0, 0x30, 0x00,
  0x17, 0xf1, 0x8f, 0xc0, 0x1f, 0x00, 0x03, 0xf1, 0x8f, 0x80, 0x1e, 0x00, 0x01, 0xf1, 0x9f, 0x00,
  0x0c, 0x00, 0x00, 0xf1, 0x8e, 0x00, 0x18, 0x00, 0x00, 0x79, 0x9c, 0x00, 0x10, 0x00, 0x00, 0x31,
  0x80, 0x00, 0x00, 0x00, 0x00, 0x01, 0x88, 0x00, 0x00, 0x00, 0x00, 0x51, 0x82, 0x00, 0x00, 0x00,
  0x00, 0x01, 0x82, 0x00, 0x00, 0x10, 0x00, 0xa1, 0x84, 0x40, 0x00, 0x10, 0x00, 0x81, 0x85, 0x00,
  0x00, 0x00, 0x02, 0x23, 0xc0, 0x50, 0x00, 0x02, 0x00, 0xa3, 0xc5, 0x08, 0x00, 0x00, 0x0a, 0x03,
  0xc0, 0x52, 0x00, 0x00, 0x88, 0xa3, 0xe1, 0x12, 0x00, 0x00, 0x4a, 0x07, 0xe1, 0x24, 0x40, 0x00,
  0x10, 0x87, 0xf0, 0x91, 0x00, 0x01, 0x4a, 0x0f, 0xf8, 0x25, 0x00, 0x00, 0x10, 0x0f, 0xf8, 0x21,
  0x40, 0x05, 0x4a, 0x1f, 0xfc, 0x0a, 0x10, 0x00, 0x10, 0x3f, 0xfe, 0x02, 0x80, 0x15, 0x48, 0x7f,
  0xff, 0x08, 0x54, 0x01, 0x10, 0xff, 0xff, 0x85, 0x00, 0x54, 0x81, 0xff, 0xff, 0xc0, 0x55, 0x01,
  0x03, 0xff, 0xff, 0xe0, 0x10, 0xa8, 0x07, 0xff, 0xff, 0xf8, 0x01, 0x00, 0x1f, 0xff, 0xff, 0xfe,
  0x00, 0x00, 0x7f, 0xff, 0xff, 0xff, 0xc0, 0x07, 0xff, 0xff, 0xff, 0xff, 0xff, 0xff, 0xff, 0xff
};

/*-----( Declare objects )-----*/
//Initialise display library with no reset pin by passing it -1
Adafruit_SSD1306 display(-1);

#if (SSD1306_LCDHEIGHT != 48)
#error("Height incorrect, please fix Adafruit_SSD1306.h!");
#endif

/*-----( Declare Variables )-----*/
int buttonState = 0; // state of on-module button
int relayState = 0;

long lastDebounceTime = 0;  // the last time the output pin was toggled


void setup() { /****** SETUP: RUNS ONCE ******/

  //setup GPIO
  pinMode(LED1, OUTPUT);
  pinMode(LED2, OUTPUT);
  pinMode(LED3, OUTPUT);
  pinMode(enableRelay, OUTPUT);
  pinMode(button, INPUT_PULLUP);

  Serial.begin(9600);

  // generate display voltage from 3V3 rail
  display.begin(SSD1306_SWITCHCAPVCC, 0x3C);  // initialize with the I2C addr 0x3C (for the 64x48)

  display.setRotation(2);
  display.clearDisplay();
  // display init complete

  display.drawBitmap(8, 0, logo_bmp, 48, 48, 1);
  display.display();
  delay(1000);

  display.setTextSize(1);
  display.setTextColor(WHITE);

  testHardware();


} //--(end setup )---

void loop() { /****** LOOP: RUNS CONSTANTLY ******/

  buttonState = !digitalRead(button);

  //filter out any noise by setting a time buffer
  if ( (millis() - lastDebounceTime) > debounceDelay) {

    //if the button has been pressed, lets toggle the LED from "off to on" or "on to off"
    if ( (buttonState == HIGH) && (relayState == 0) ) {

      digitalWrite(enableRelay, HIGH);
      relayState = 1;
      lastDebounceTime = millis();
    }
    else if ( (buttonState == HIGH) && (relayState == 1) ) {

      digitalWrite(enableRelay, LOW);
      relayState = 0;
      lastDebounceTime = millis();
    }
  }

  display.clearDisplay();
  display.setCursor(0, 0);
  display.println("*Uptime*");
  display.println("");
  display.print("Relay: ");
  display.println(relayState);
  display.print(uptime());
  display.display();

} //--(end main loop )---

/*-----( Declare User-written Functions )-----*/
void testHardware() {
  display.clearDisplay();
  display.setCursor(0, 0);
  display.println("*Testing*");

  display.print("LED1");
  display.display();
  testLED(LED1);
  display.print("LED2");
  display.display();
  testLED(LED2);
  display.print("LED3");
  display.display();
  testLED(LED3);

  delay(500);

  testRelay();

  delay(500);

}

void testLED(int pinNumber) {
  analogWrite(pinNumber, brightnessLED);
  for (int i = 0; i < 3; i++) {
    display.print(".");
    display.display();
    delay(300);
  }
  display.println("OK");
  display.display();
  analogWrite(pinNumber, 0);
  delay(200);
}

void testRelay() {
  display.clearDisplay();
  display.setCursor(0, 0);
  display.println("*Relay*");
  display.println("");
  display.print("On");
  display.display();

  digitalWrite(enableRelay, HIGH);
  for (int i = 0; i < 4; i++) {
    display.print(".");
    display.display();
    delay(300);
  }
  display.println("OK");
  display.display();
  delay(200);

  display.print("Off");

  digitalWrite(enableRelay, LOW);
  for (int i = 0; i < 3; i++) {
    display.print(".");
    display.display();
    delay(300);
  }
  display.println("OK");
  display.display();
  delay(200);
}

char *uptime() // Function made to millis() be an optional parameter
{
  return (char *)uptime(millis()); // call original uptime function with unsigned long millis() value
}

char *uptime(unsigned long milli)
{
  static char _return[32];
  unsigned long secs = milli / 1000, mins = secs / 60;
  unsigned int hours = mins / 60, days = hours / 24;
  milli -= secs * 1000;
  secs -= mins * 60;
  mins -= hours * 60;
  hours -= days * 24;
  sprintf(_return, "%2.2d days   %2.2d:%2.2d:%2.2d", (byte)days, (byte)hours, (byte)mins, (byte)secs, (int)milli);
  return _return;
}

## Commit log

2023-03-07 added hardware
    [Bill of Materials.xlsx, CUI_DEVICES_TBP03R1-350-04BE.step, CUI_DEVICES_TBP03R1-350-06BE.step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]
2023-03-07 Added more detail about the enclosure
2025-11-29 started work on new rev
    [roller-shutter-controller.kicad_pcb, roller-shutter-controller.kicad_sch]
2025-11-29 first draft of v4 schematic
    [roller-shutter-controller.kicad_pcb, roller-shutter-controller.kicad_sch]
2025-12-06 forgot to git add everything..
    [Bill of Materials.xlsx, microcontroller.kicad_sch]
2026-01-23 swapped DC-DCs, upgraded to S3
    [microcontroller.kicad_sch, roller-shutter-controller.kicad_sch]
2026-01-25 schematic WIP
    [microcontroller.kicad_sch, power.kicad_sch, roller-shutter-controller.kicad_sch]
